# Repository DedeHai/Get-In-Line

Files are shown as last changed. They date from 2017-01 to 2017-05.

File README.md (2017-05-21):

# Get In Line - line-following robot
Simple line following robot using a single break-away PCB design. Using mostly 0805-components to make it easier to solder by hand. Four potentiometers at the bottom let you change the speed and regulator settings without re-programming the microcontroller. 
More information available at https://bashtelorofscience.wordpress.com/ 

License:
Software under MIT license
Hardware under Creative Commons 4.0 license: CC-BY-NC-SA

# Software
The PCB was designed in **eagle** version 7.5.0. The firmware project was created using **System Workbench for STM32** and **STM32CubeMX**.

# Fotos
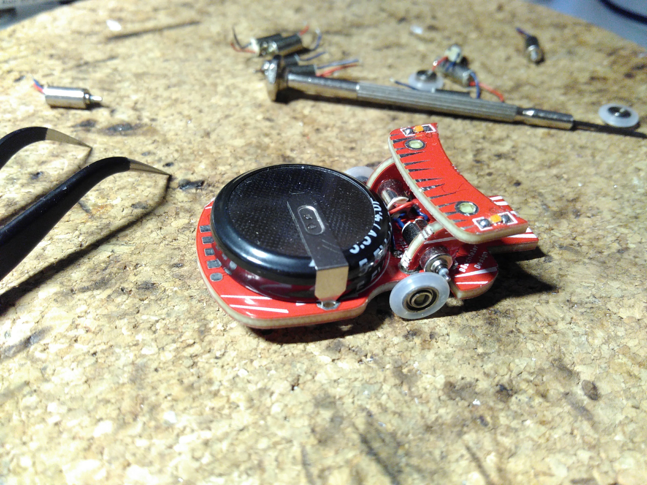
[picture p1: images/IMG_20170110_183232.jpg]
First Prototype Top
 
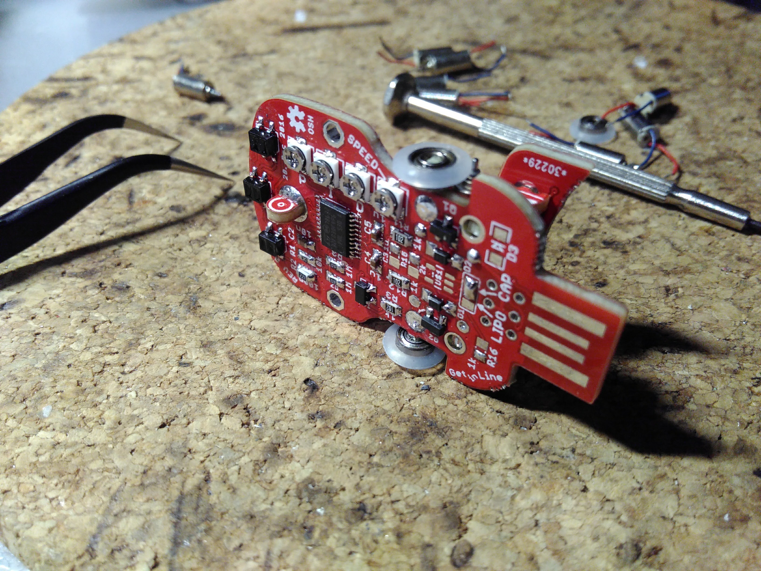
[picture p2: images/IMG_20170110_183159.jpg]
First Prototype Bottom
 
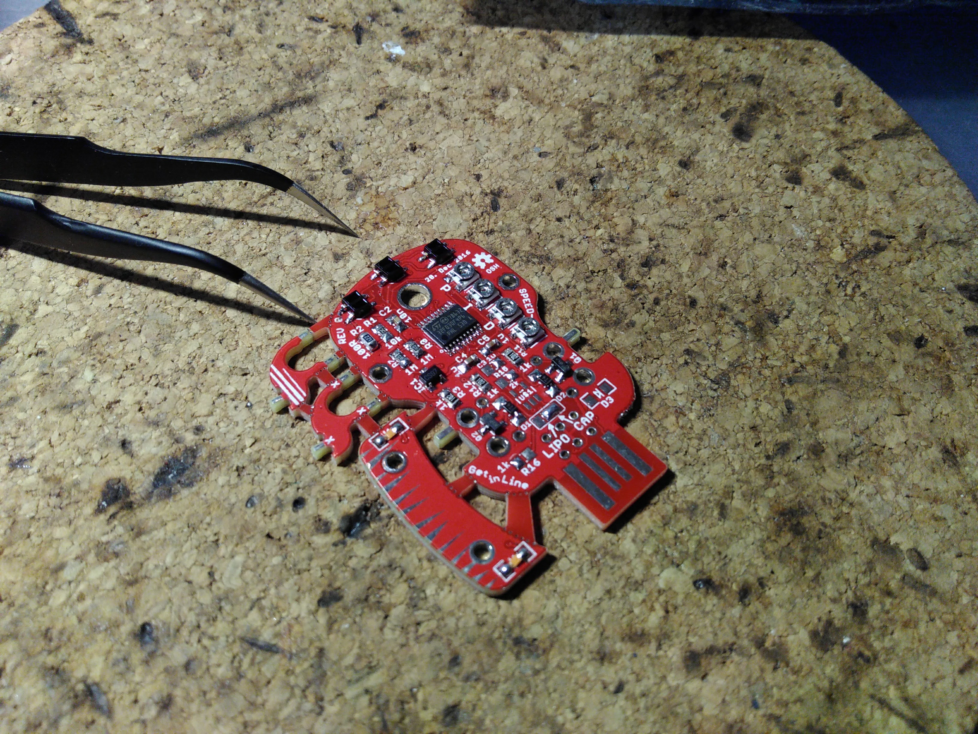
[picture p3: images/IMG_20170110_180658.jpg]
First Prototype Soldered


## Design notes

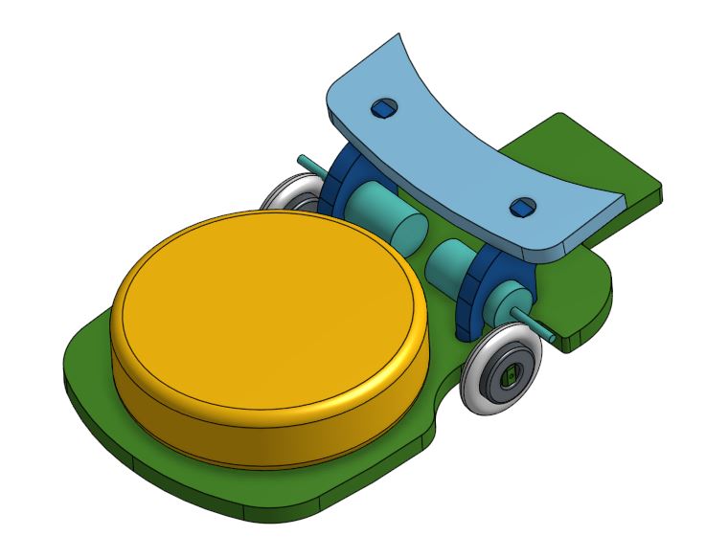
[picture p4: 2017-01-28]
Hardware/Get_In_Line_REV0_3D-view-mechanical.JPG

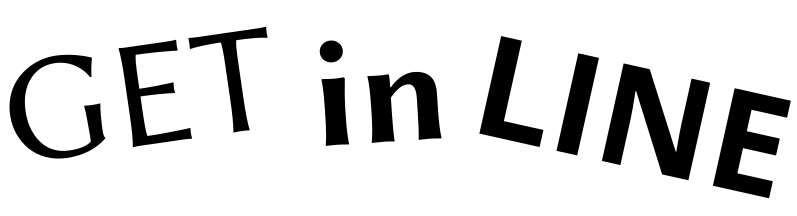
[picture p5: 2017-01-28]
Hardware/getinline.PNG

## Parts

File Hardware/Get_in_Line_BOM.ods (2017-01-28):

GET IN LINE – line follower robot Bill of Materials
Part | Order price | Pieces per order | Piecer per bot | Price per bot
PCB | 15 | 10 | 1 | 1.5 | http://dirtypcbs.com/store/pcbs
Bearings – MR52ZZ | 3.41 | 10 | 2 | 0.68 | http://www.banggood.com/10pcs-MR52ZZ-Double-Shielded-Deep-Groove-Ball-Miniature-Bearings-p-78792.html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
Rubber O ring | 2.38 | 150 | 2 | 0.03 | http://www.banggood.com/150pcs-White-O-Ring-Keycap-Rubber-For-Cherry-MX-Switch-Keyboard-p-937511.html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
Motor | 4.16 | 10 | 2 | 0.83 | http://www.banggood.com/10pcs-4x8mm-DC1_5-3V-Micro-Coreless-Motor-Vibration-Motor-p-999837.html?rmmds=myorder
Motor, better quality | 7 | 10 | 2 | 1.4 | https://www.aliexpress.com/item/good-quality-10pcs-408-dc-Coreless-Motor-for-helicopter-ailplanes-aircraf-high-speed-4x8mm/32261734792.html
Switch | 1.87 | 20 | 1 | 0.09 | https://www.aliexpress.com/item/WSFS-Wholesale-2-X-20-Pcs-On-Off-On-DPDT-2P2T-6-Pin-Vertical-DIP-Slide/32578250645.html
Trimmer Potentiometer | 4.7 | 50 | 4 | 0.38 | https://www.aliexpress.com/store/product/100PCS-3-3-3-3-3x3-5K-ohm-patch-adjustable-potentiometer/511081_32583469520.html
QRE1113 Reflective Sensor | 11 | 50 | 3 | 0.66 | https://www.aliexpress.com/item/Free-shipping-100pcs-lot-QRE1113GR-QRE1113-QRE1113G-SENSOR-OPTO-TRANS-REFL-SMD-PHOTO-Best-quality/32760197560.html
NPN transistor | 1.27 | 100 | 2 | 0.03 | https://www.aliexpress.com/item/Y111-MMBT2222A-100-PCS-SOT-23-MMBT2222-2N2222-SMD-General-Purpose-Transistors-NPN-40V-0-6A/32311239794.html
1N4148 Diode | 0.6 | 100 | 2 | 0.01 | https://www.aliexpress.com/item/Free-Shipping-100pcs-1N4148-LL4148-SMD-SMT-Diode-Switching-Signal/664923038.html
XC6206P332 3.3V Regulator | 1.4 | 50 | 1 | 0.03 | https://www.aliexpress.com/item/50pcs-free-shipping-XC6206P332MR-662K-XC6206-3-3V-0-5A-Positive-Fixed-LDO-Voltage-Regulator-SOT/32426685794.html
Resistor, 1k | 0.42 | 100 | 4 | 0.02 | https://www.aliexpress.com/store/product/100pcs-lot-SMD-Chip-Resistor-1-0805-1K-1K-1-8W-100-YAGEO-New-Original-Chip/1361740_32570151447.html
Resistor, 10k | 0.42 | 100 | 1 | 0 | https://www.aliexpress.com/store/product/100pcs-lot-SMD-Chip-Resistor-1-0805-10K-1-8W-100-YAGEO-New-Original-Chip-Fixed/1361740_32569368590.html
Resistor, 1M | 0.42 | 100 | 2 | 0.01 | https://www.aliexpress.com/store/product/100pcs-lot-SMD-Chip-Resistor-1-0805-1M-1-8W-100-YAGEO-New-Original-Chip-Fixed/1361740_32569356535.html
Resistor, 100R | 0.42 | 100 | 1 | 0 | https://www.aliexpress.com/store/product/100pcs-lot-SMD-Chip-Resistor-1-0805-100R-100-OHMS-1-8W-100-YAGEO-New-Original/1361740_32568098663.html
Resistor, 2k | 0.42 | 100 | 1 | 0 | https://www.aliexpress.com/store/product/100pcs-lot-SMD-Chip-Resistor-1-0805-2K-2K-1-8W-100-YAGEO-New-Original-Chip/1361740_32569396331.html
Capacitor, 100nF | 0.6 | 100 | 1 | 0.01 | https://www.aliexpress.com/store/product/Free-shipping-100pcs-lot-0805-100nF-104K-0-1uF-50V-X7R-10-2012-SMD-Multilayer-Ceramic/1361740_32677815090.html
Capacitor, 10uF, 10V | 1.82 | 100 | 3 | 0.05 | https://www.aliexpress.com/store/product/Free-shipping-100pcs-lot-0805-10uF-106K-25V-X7R-10-2012-SMD-Multilayer-Ceramic-Chip-Capacitor/1361740_32677028139.html
LED 1206 (any color) | 1.43 | 100 | 3 | 0.04 | https://www.aliexpress.com/item/100pcs-lot-1206-SMD-LED-light-Package-LED-Package-Red-White-Green-Blue-Yellow-1206-led/32668226209.html
STM32F03F4P6 Microcontroller | 4.3 | 10 | 1 | 0.43 | https://www.aliexpress.com/item/Free-shipping-10pcs-Lot-STM32F030F4P6-STM32F030F/1899750362.html
TP4054 LiPo Charger | 3.6 | 20 | 1 | 0.18 | https://www.aliexpress.com/item/TP4054-new-original-printing-54b-lithium-rechargeable-IC-package-SOT23-5-SZHQDZ/32712500075.html
LiPo Battery (20x30mm max size) | 14 | 10 | 1 | 1.4 | https://www.aliexpress.com/item/3-7V-150mAh-Syma-S107-S107G-1S-3-7V-150mAh-Li-Po-Battery-3-7V-Helicopter/32752994770.html
 | 80.64 |  |  | 7.79
Optional
Programmer
ST-Link clone (Programmer) | 2.2 | 1 |  |  | https://www.aliexpress.com/item/Hot-Sale-1PCS-ST-LINK-Stlink-ST-Link-V2-Mini-STM8-STM32-Simulator-Download-Programmer-Programming/32343514985.html
SuperCap (very short working time!) | 2.76 | 2 | 1 | 1.38 | https://www.aliexpress.com/item/2Pcs-ultra-capacitor-5-5v4f-super-capacitor-H-style-For-promotion-Now-Lowest-Price/32571210201.html
Resistors, various (kit) | 2.2 | 50 | 15 | 0.66 | https://www.aliexpress.com/item/Free-shipping-0805-5-SMD-Resistor-Kit-0R-10M-36valuesX20pcs-720pcs-Chip-Resistor-sample-kit/32695511447.html
Capacitor, various (kit) | 2.7 | 10 | 2 | 0.54 | https://www.aliexpress.com/item/Free-shipping-0805-SMD-Capacitor-29valuesX10pcs-290pcs-Chip-Capacitor-Electronic-Components-Package-Samples-kit/773778463.html

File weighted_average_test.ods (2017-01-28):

Position | Value | Weighted value
7500 | 200 | 1500000
15000 | 400 | 6000000
22500 | 135 | 3037500
 |  |  | Line center position:
sum: | 735 | 10537500 | 14336.7346938776
Center aligned:
-7500
0
7500 |  |  | -663.2653061224

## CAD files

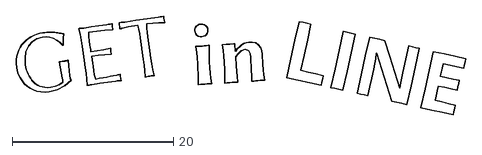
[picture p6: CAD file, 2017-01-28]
Hardware/getinline_writing.dxf
55.8 x 12.3

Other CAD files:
Hardware/getinline.dxf

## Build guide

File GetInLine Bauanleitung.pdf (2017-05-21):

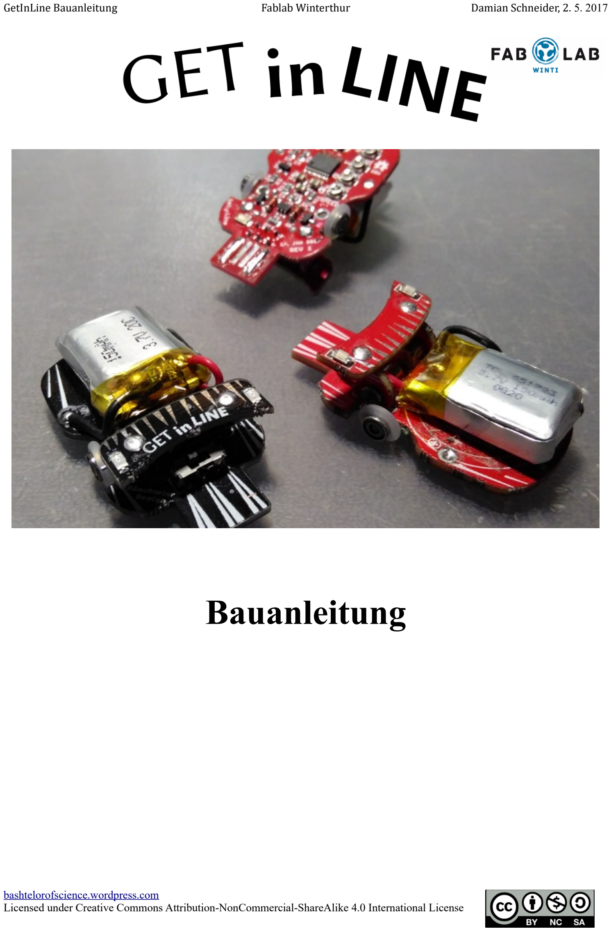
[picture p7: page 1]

GetInLine Bauanleitung | Fablab Winterthur | Damian Schneider, 2. 5. 2017

# Bauanleitung

bashtelorofscience.wordpress.com
Licensed under Creative Commons Attribution-NonCommercial-ShareAlike 4.0 International License

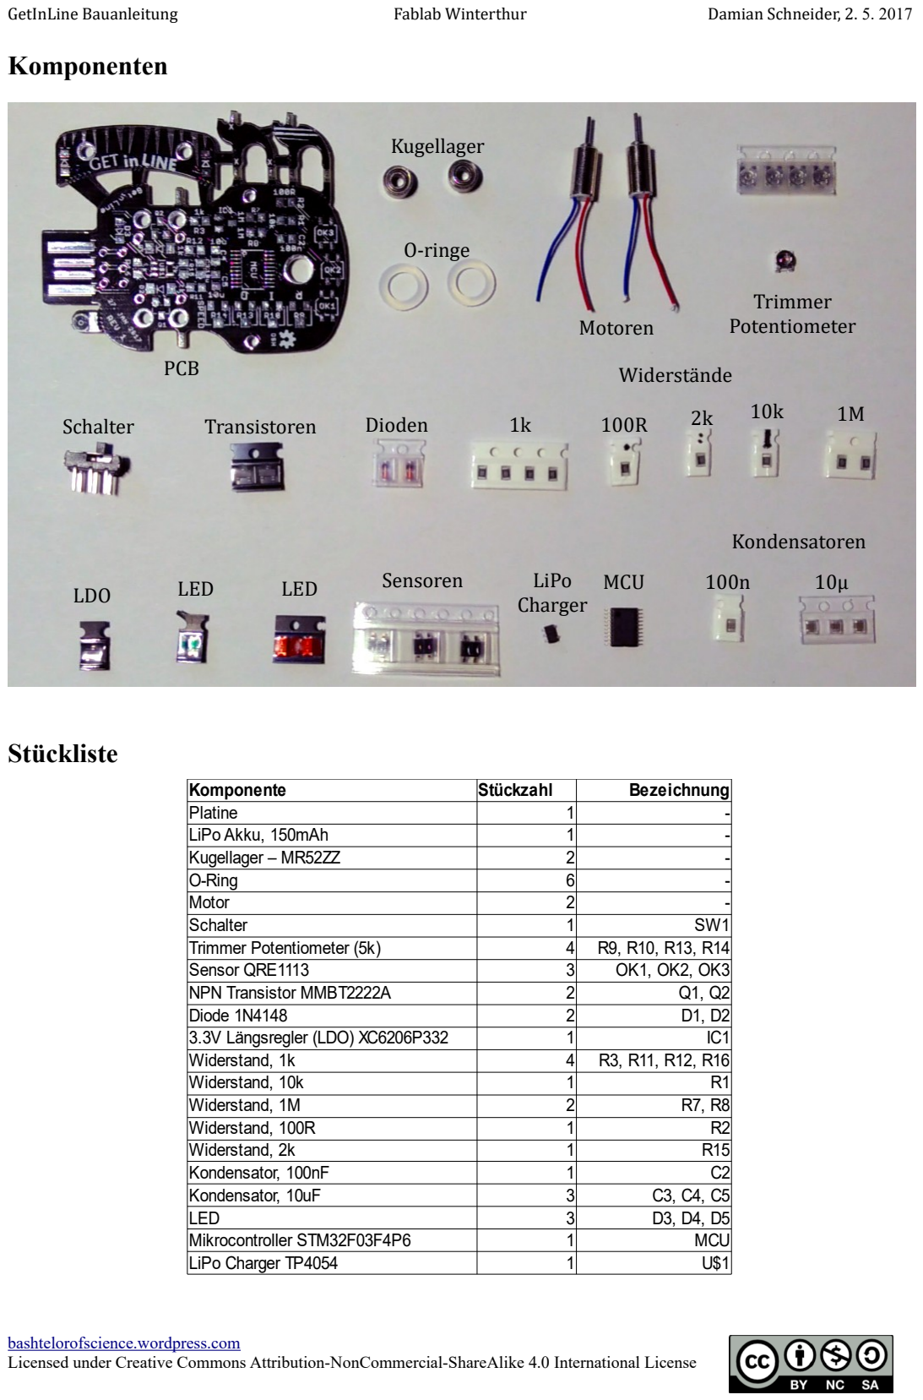
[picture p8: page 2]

Komponenten

Stückliste

bashtelorofscience.wordpress.com

Komponente | Stückzahl | Bezeichnung
Platine | 1 | -
LiPo Akku, 150mAh | 1 | -
Kugellager – MR52ZZ | 2 | -
O-Ring | 6 | -
Motor | 2 | -
Schalter | 1 | SW1
Trimmer Potentiometer (5k) | 4 | R9, R10, R13, R14
Sensor QRE1113 | 3 | OK1, OK2, OK3
NPN Transistor MMBT2222A | 2 | Q1, Q2
Diode 1N4148 | 2 | D1, D2
3.3V Längsregler (LDO) XC6206P332 | 1 | IC1
Widerstand, 1k | 4 | R3, R11, R12, R16
Widerstand, 10k | 1 | R1
Widerstand, 1M | 2 | R7, R8
Widerstand, 100R | 1 | R2
Widerstand, 2k | 1 | R15
Kondensator, 100nF | 1 | C2
Kondensator, 10uF | 3 | C3, C4, C5
LED | 3 | D3, D4, D5
Mikrocontroller STM32F03F4P6 | 1 | MCU
LiPo Charger TP4054 | 1 | U$1

Kugellager

O-ringe

PCB

Motoren

Trimmer
Potentiometer
Schalter | Transistoren | Dioden

Widerstaände
1k | 100R | 2k | 10k | 1M

Kondensatoren
LiPo | MCU | 100n | 10µ
Charger

Sensoren
LDO | LED | LED

Bestückungsplan

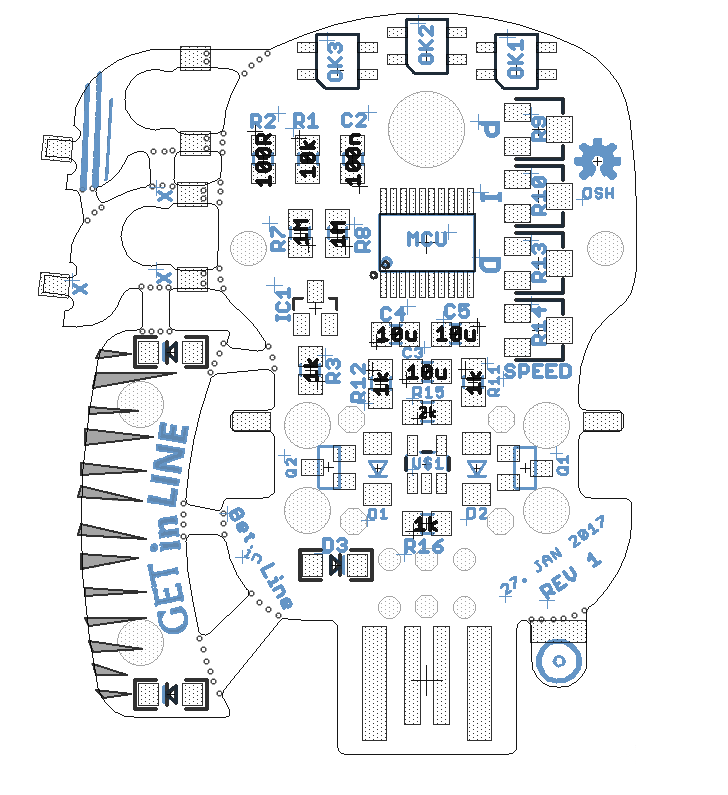
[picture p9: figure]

bashtelorofscience.wordpress.com

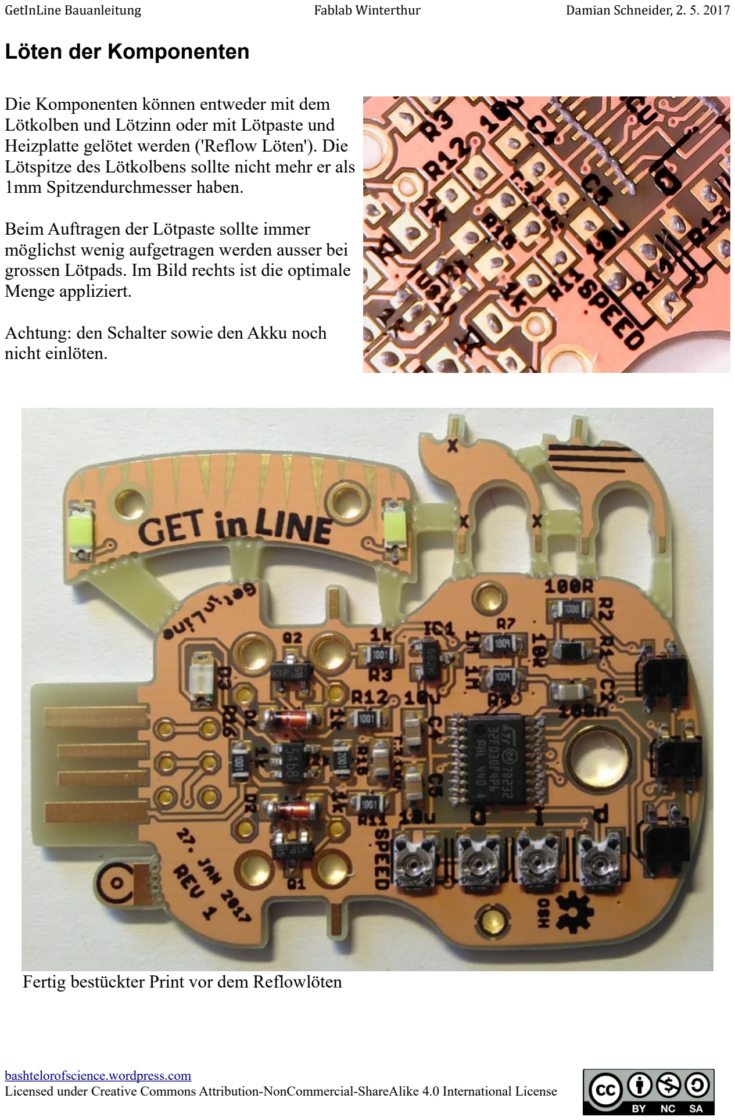
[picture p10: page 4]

Löten der Komponenten

Die Komponenten können entweder mit dem Lötkolben und Lötzinn oder mit Lötpaste und Heizplatte gelötet werden ('Reflow Löten'). Die Lötspitze des Lötkolbens sollte nicht mehr er als 1mm Spitzendurchmesser haben.

Beim Auftragen der Lötpaste sollte immer möglichst wenig aufgetragen werden ausser bei grossen Lötpads. Im Bild rechts ist die optimale Menge appliziert.

Achtung: den Schalter sowie den Akku noch nicht einlöten.

Fertig bestückter Print vor dem Reflowlöten

bashtelorofscience.wordpress.com

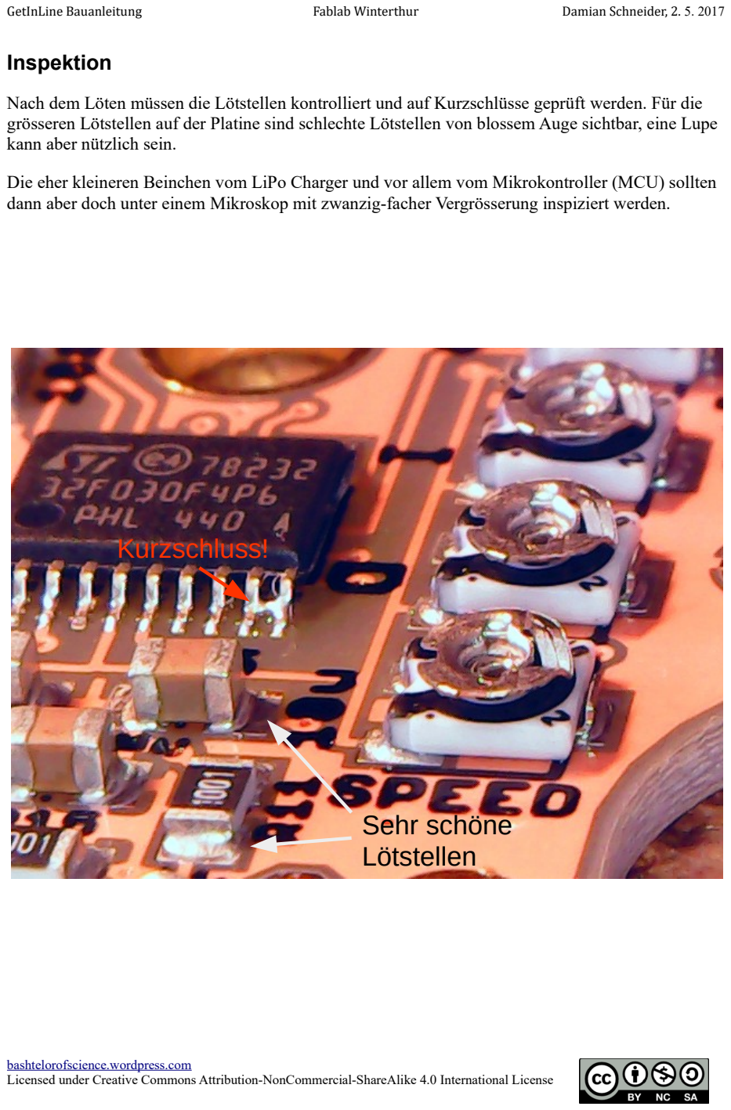
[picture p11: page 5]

Inspektion

Nach dem Löten müssen die Lötstellen kontrolliert und auf Kurzschlüsse geprüft werden. Für die grösseren Lötstellen auf der Platine sind schlechte Lötstellen von blossem Auge sichtbar, eine Lupe kann aber nützlich sein.

Die eher kleineren Beinchen vom LiPo Charger und vor allem vom Mikrokontroller (MCU) sollten dann aber doch unter einem Mikroskop mit zwanzig-facher Vergrösserung inspiziert werden.

bashtelorofscience.wordpress.com

## Kurzschluss!

## Sehr schöne Lötstellen

Roboter Montage
Bitte jeden Abschnitt zuerst komplett durchlesen und erst dann ausführen um mühsames Entlöten oder gar Zerstörung des Prints zu vermeiden.
Als erstes müssen die einzelnen Teile der Platine vorsichtig auseinander gebrochen werden. Die feineren Stege knippst man am einfachsten mit einem feinen Seitenschneider möglichst nahe an der Hauptplatine durch. Die perforierten stellen können auch gebrochen werden, dazu sollte man immer zwei Zangen verwenden um die dünnen Teile nicht zu verbiegen oder gar zu brechen. Die etwas unschönen Bruchstellen können gut mit einer Schlüsselfeile oder mit einem Messer nachbearbeitet werden.

Vorderrad einlöten: mit dem Print auf der Lötunterlage das Rad wie in den Bildern gezeigt ausrichten und mit viel Lötzinn einlöten. Dabei ist darauf zu achten, dass das Lötzinn sowohl das Loch wie auch das 'Rad' gut benetzt.

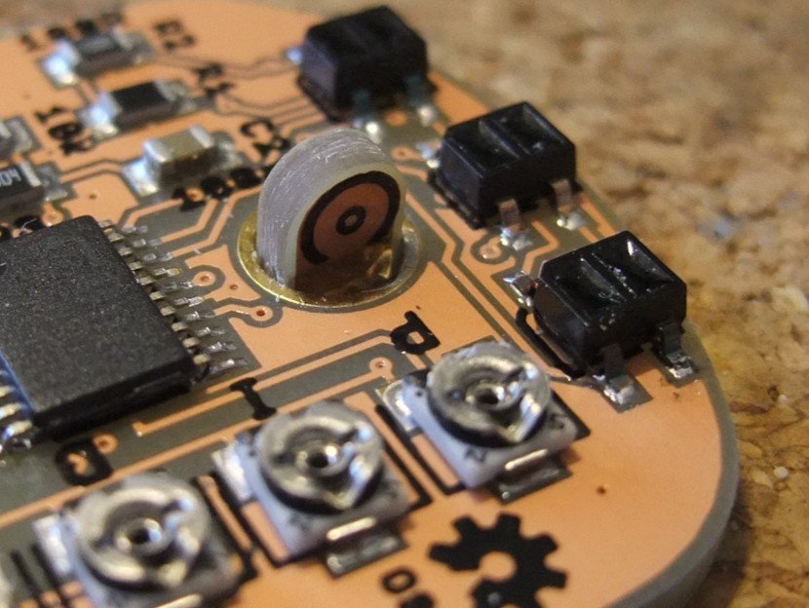
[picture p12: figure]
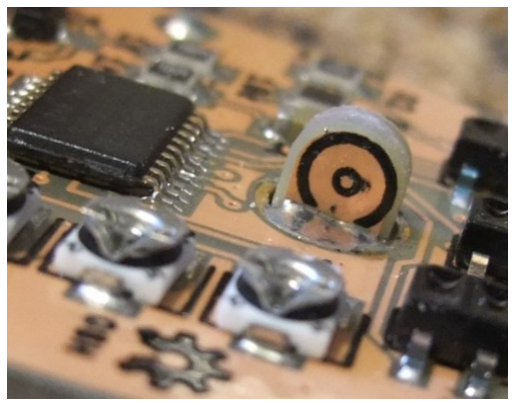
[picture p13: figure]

Vorderrad ausgerichtet… | …und gelötet

Spoiler Ausrichten: die beiden Seitenwände entsprechend den Markierungen X und Y einstecken und den Spoiler oben drauf montieren. Sobald alles schön passt kann der Spoiler von oben an die Seitenwände angelötet werden. Dabei ist es wichtig genügen lange mit dem Lötkolben zu heizen. Die Seitenwände nicht mit der Hauptplatine verlöten! Jetzt wird der Spoiler zusammen mit den Seitenwänden wieder entfernt um die Motoren einzusetzen.

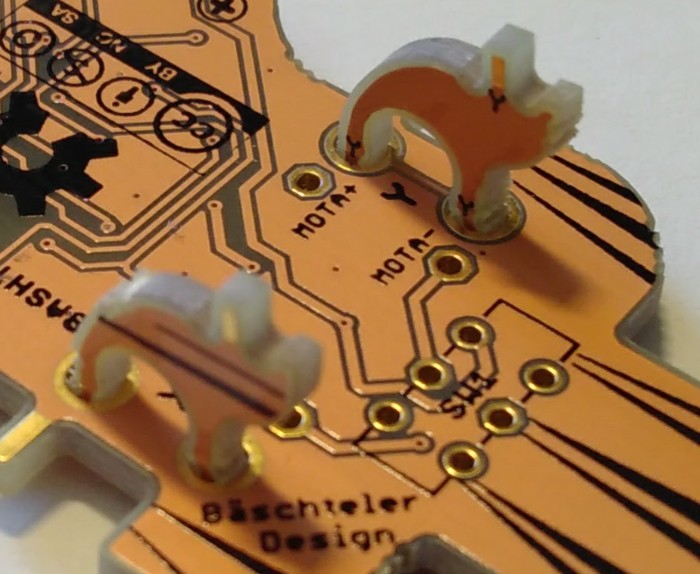
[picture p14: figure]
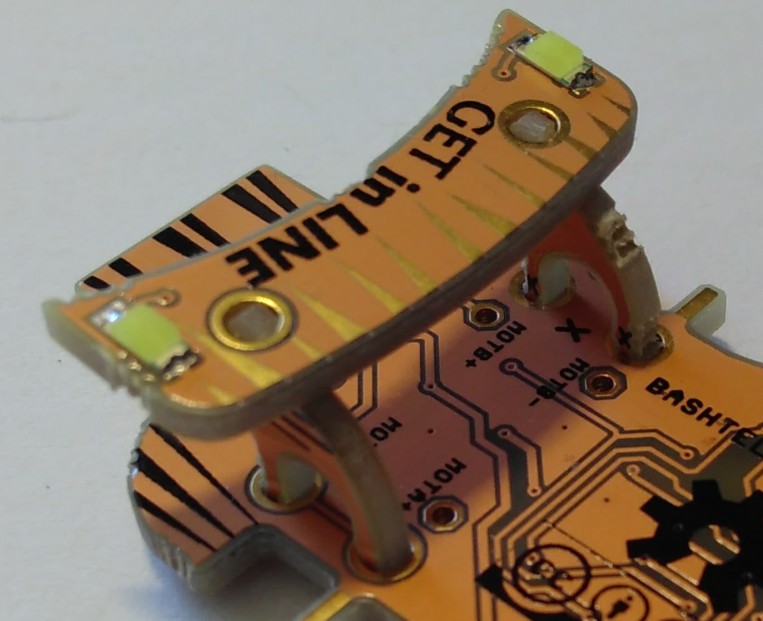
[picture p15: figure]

Positionieren der Seitenwände und des Spoilers

Schalter löten: der Schalter kommt auf die Oberseite, da wo der Print mit ‚SW1‘ markiert ist.

bashtelorofscience.wordpress.com

Motoren einsetzen: die Kabel der Motoren auf eine Länge von ca. 2cm kürzen, abisolieren und verzinnen. Danach beide Motoren von aussen her in die Öffnungen der Seitenwände einschieben. Das benötigt etwas kraft. Vorsicht: die dünnen Beine der Seitenwände brechen leicht ab. Die Motoren vorerst etwa mittig platzieren und so drehen, dass die Kabel wie auf dem Bild gezeigt ausgerichtet sind (nicht an den kabeln ziehen!). Jetzt können die Kabel eingelötet werden. Dabei die Polarität beachten: blau auf minus, rot auf plus, wie im rechten Foto.

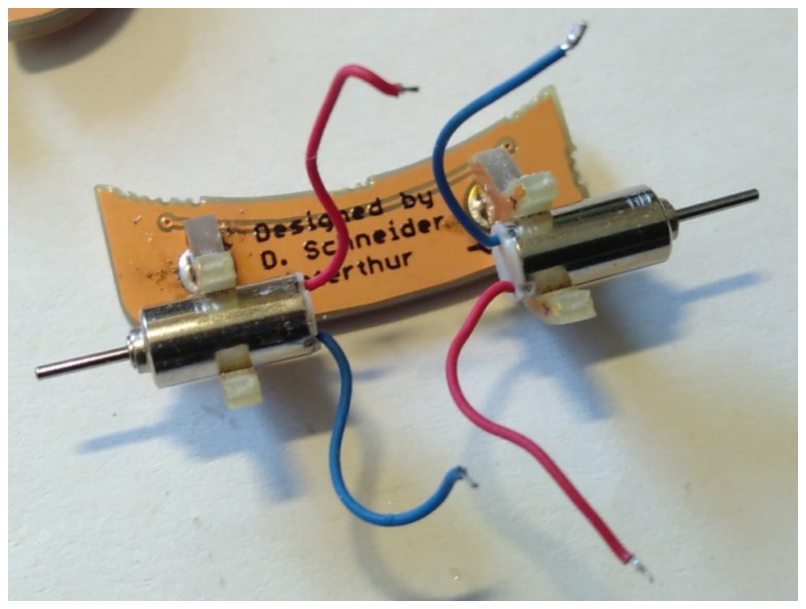
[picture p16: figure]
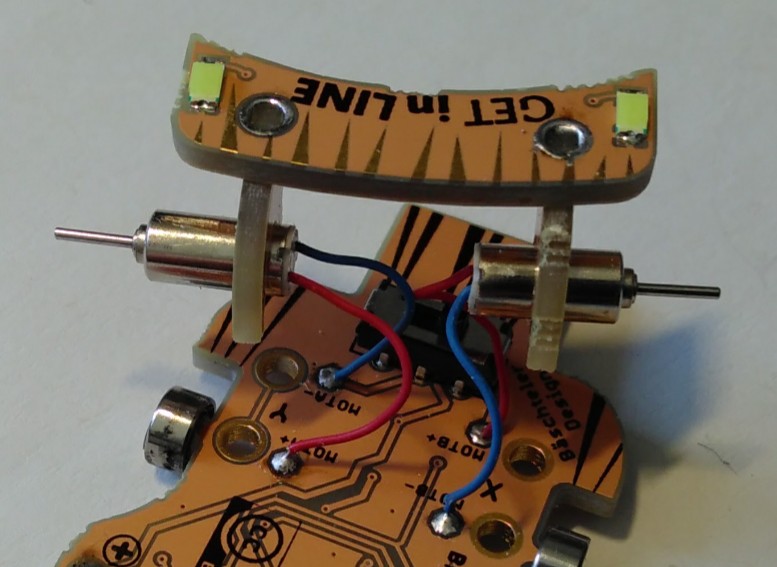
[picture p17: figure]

Motoren eingesetzt, Kabel ausgerichtet | und eingelötet

Akku löten: Den Schalter auf Position ‚Aus‘ stellen (wie im Foto unten). Den Akku mit der richtigen Polarität einlöten. Die Isolation am positiven Kabel erst kurz vor dem Löten des Kabels entfernen, der Akku hat viel Leistung und kann bei Kurzschlüssen über die Platine auch Leiterbahnen schmelzen!
Kugellager einpressen: die beiden Kugellager können einfach mit etwas Kraftaufwand aufgesteckt werden und sollten dann gut halten. Allenfalls mit einem Zahnstocher ganz wenig Sekundenkleber auftragen.

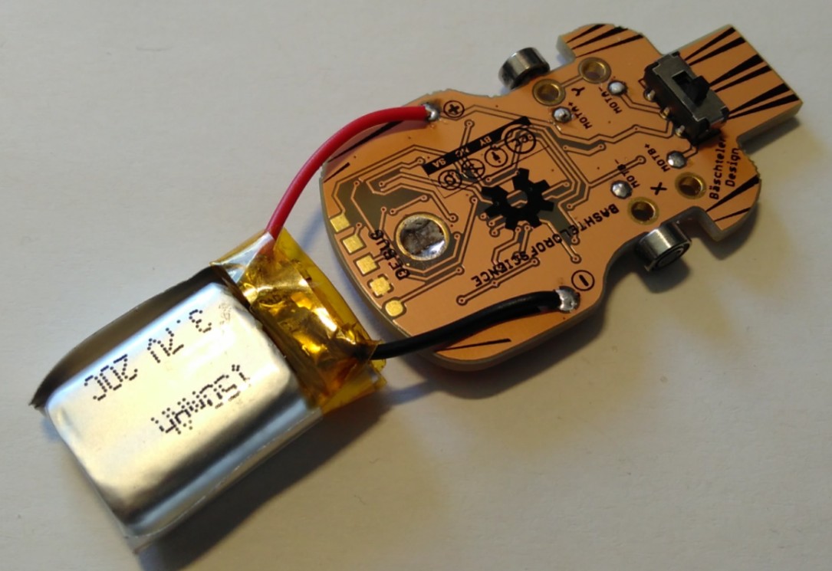
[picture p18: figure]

Schalter und Akku angelötet, Kugellager aufgesetzt (Motoren fehlen auf dem Bild)

bashtelorofscience.wordpress.com

O-Ringe aufsetzen: aus den O-ringen zwei auswählen die möglichst keine Brauen auf der Lauffläche haben und auf die Kugellager aufsetzen. Brauen allenfalls mit einer Pinzette entfernen.

Drehrichtung prüfen: den Roboter einschalten und die Motoren von Hand leicht auf die O-ringe drücken. Die Drehrichtung der Räder muss so sein, wie es in den Abbildungen mit Pfeilen angedeutet ist. Der Roboter soll sich ja später vorwärts bewegen. Stimmt die Drehrichtung nicht müssen die Motoranschlüsse andersrum gelötet werden.

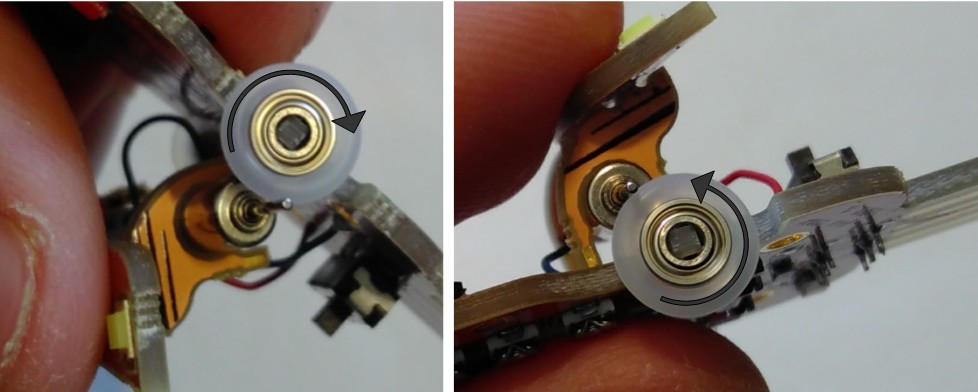
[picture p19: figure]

Motortest: Drehrichtungen

Motren ausrichten: Die Motoren werden in den Seitenwänden so ausgerichtet, dass sie aussen bündig sowie gerade und auf einer Linie sind (siehe Foto). Die Motorkabel alle nach aussen biegen, damit sie beim Einsetzen nicht unter die Motoren zu liegen kommen. Jetzt kann die Motoreinheit eingesetzt werden. An dieser Stelle ist es wichtig, die Anpresskraft der Motoren auf die O-Ringe möglichst gut einzustellen. Kleine Korrekturen sind zwar später noch möglich aber je besser die Motoreinheit vor dem Verlöten ausgerichtet ist, desto besser funktioniert am Ende der Roboter.
Die Motoren müssen auf der Platine aufliegen.

Einstellen der Anpresskraft: dieser Schritt ist entscheidend damit der Roboter gut funktioniert. Wenn die Motoreinheit richtig sitzt kann die Anpresskraft durch kippen eingestellt werden. Die Kraft sollte so gering wie möglich sein aber nicht so, dass beim Stoppen des Rads von Hand der Motor durchdreht und nicht so stark, dass der Motor nach dem Stoppen nicht selbständig wieder anläuft. Wenn die Motoren auf einer Linie ausgerichtet wurden sollte es möglich sein, beide Seiten gleichzeitig auszurichten.

bashtelorofscience.wordpress.com

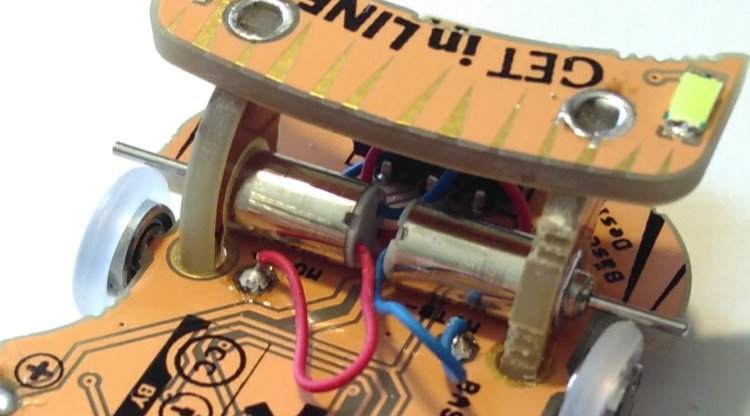
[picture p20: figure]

Anpressdruck gut eingestellt

Seitenwände Löten: mit laufenden Motoren den Roboter vorsichtig mit dem Spoiler nach unten auf die Lötunterlage legen. Die Anpresskraft noch einmal überprüfen (Räder stoppen). Die beiden Lötstellen die mit grünen Pfeilen Markiert sind löten (eventuell grössere Lötspitze benutzen) und dabei möglichst keine Kraft aufwenden, ansonsten wird die Motoreinheit verschoben und muss wieder ausgerichtet werden. Achtung: werden auch die Lötstellen mit den roten Kreuzen gelötet, ist ein erneutes ausrichten der Motoren schwierig. Beim Löten genügend Lötzinn verwenden und mindestens 5 Sekunden aufheizen. Beim löten der zweiten Seitenwand sollten die beiden LEDs auf dem Spoiler anfangen zu leuchten.

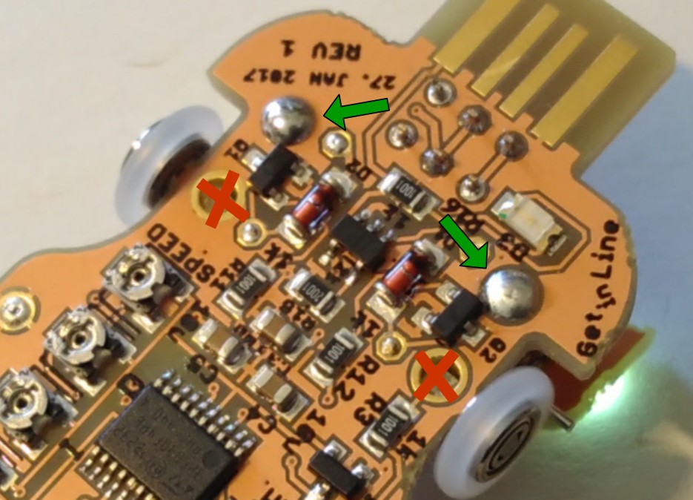
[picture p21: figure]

Seitenwände gelötet und die LEDs leuchten bereits

Erste Testfahrt: Jetzt kannst du den Akku richtig platzieren und schon kanns los gehen mit der ersten Testfahrt. Schalte den Roboter aus und setzte ihn auf eine Teststrecke. Bei jedem Einschalten

bashtelorofscience.wordpress.com werden die Sensoren automatisch kalibriert. Wenn alles gut funktioniert und kein weiteres Ausrichten der Motoren nötig ist können nun auch noch die anderen beiden Lötstellen der Seitenwände gelötet werden.

Letze Anpassungen: wenn alles ok ist, kannst du jetzt die zweite Lötstelle der Seitenwände verlöten. Auch hier wieder genügend Zinn verwenden und mindestens 5 Sekunden heizen. Die Anpresskraft kann nun noch folgendermassen Feinjustiert werden: mit einem kleinen Schraubenzieher (nicht mit der Pinzette!) auf den Motor drücken, bis die Anpresskraft stimmt. Achtung: nicht auf die Kabel drücken, diese können schnell reissen.
Den Akku klebt man am besten mit doppelseitigem Klebeband fest oder mit etwas Heissleim. Damit das Aufladen am USB-Port gut funktioniert müssen noch die beiden äusseren Pads vom USB-Stecker dick verzinnt werden.

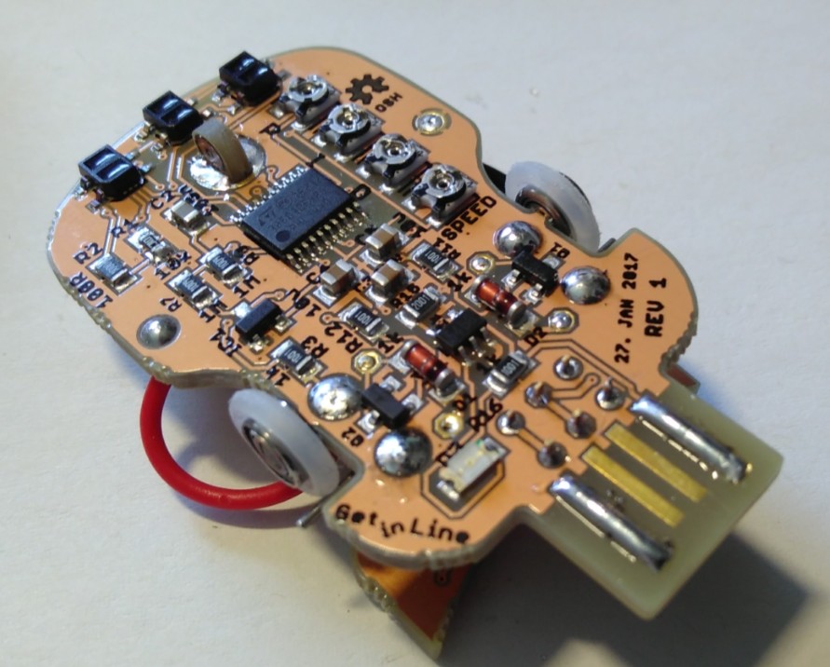
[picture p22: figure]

Fertig zusammengebauter Roboter

Einstellen der Regelung
Mit allen Potentiometer auf Mittelstellung fährt der Roboter eigentlich schon ganz gut. Man kann die Regelung aber auch noch optimieren damit der Roboter möglichst schnell oder möglichst ruhig fährt.

bashtelorofscience.wordpress.com

Die Potentiometer sind mit P, I, D und SPEED angeschrieben.

P: Proportional Anteil des Reglers - Gegensteuer bei Abweichung vom Sollsignal. Zu hoch und der Roboter oszilliert mit schnellen Schwenkern. Wenn der Wert zu tief ist übernimmt der Integral Anteil die Regelung und der Roboter 'schlängelt' über den Pfad.

I: Integralanteil des Reglers - die Regelabweichung wird aufsummiert um kleine Fehler zu korrigieren, auf die der proportionale Anteil zu wenig reagiert.

D: Differentialanteil des Reglers - dieser beugt Übersteuerungen vor und dämpft Oszillationen etwas indem er kurzfristig dem Integralanteil entgegenwirkt.

SPEED: das "Gaspedal". Ist die Geschwindigkeit zu tief eingestellt, fährt der Roboter gar nicht oder bleibt dauernd stehen. Zu hohe Geschwindigkeiten bereiten dem Regler mühe und in den Kurven schiesst er aus der Bahn - der Roboter hat keine Bremse! Für eine ruhige Fahrt sollte die Geschwindigkeit so tief wie möglich eingestellt sein.

bashtelorofscience.wordpress.com

## Appendix: SMD Bauteilgehäuse

SMD Komponenten kommen in hunderten von verschiedenen Gehäusen. Viele davon sind Genormt aber diverse Hersteller haben auch noch ihre eigenen Varianten davon, als Beispiel sei hier der Sensor QRE1113 von ON-Semiconductor (früher Fairchild) angeführt, der ein Spezialgehäuse gepackt ist.
Gehäuse von Widerständen, Kondensatoren und LEDs sowie weitere zweipolige Komponenten werden mit der Grössenangabe in hundertstel Zoll angegeben. Gängige Bauteilgrössen in Absteigender Reihenfolge sind 1210, 1206, 0805, 0603, 0402 und 0201. Bis zur Grösse von 0603 kann gut von Hand gelötet werden, 0402 geht gerade noch unter dem Mikroskop und bei 0201 wird’s eher knifflig, ist aber nicht unmöglich. Die hier verwendeten Widerstände und Kondensatoren sind in der Grösse 0805 (0.08x0.05 Zoll oder 2x1.27mm) und die LEDs sind in 1206 Gehäusen untergebracht.
Symmetrische Bauteile die eine Ausrichtung benötigen haben immer eine Kennzeichnung an einem der Anschlüsse. Fast ausnahmslos ist Pin eins mit einem Punkt oder einer angeschrägten Ecke oder Kante markiert. Bei LEDs ist häufig die Kathode mit einem grünen Punkt markiert oder man findet ein Symbol auf der Unterseite (oder beides). Bei asymmetrischen Bauteilen ist die Ausrichtung ohnehin klar und eine Markierung ist optional.

Widerstände
Bei Widerständen gibt es bei SMD Bauteilen im Gegensatz zur bedrahteten Version keine Farbcodes mehr. Stattdessen ist der Widerstandswert in Zahlen aufgedruckt. Dabei bezeichnen die ersten Ziffern den Widerstandswert und die letzte Ziffer die Zehnerpotenz. Für die hier abgebildeten Widerstände bedeutet dies:
1000 → 100*10⁰
= 100Ω
2001 → 200*10¹
= 2000Ω = 2kΩ
1004 → 100*10⁴
= 1000000Ω = 1MΩ

LED/Dioden

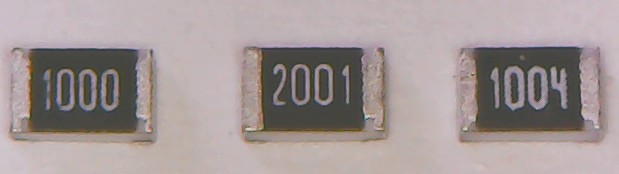
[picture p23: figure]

Dioden haben wie immer eine Markierung auf der Kathodenseite. Im allgemeinen ist dies eine Linie, kann aber auch ein Punkt sein. Bei LEDs gibt es oft (zusätzlich) ein 'Dreieck' Symbol auf der Unterseite, welches das Dreieck im Diodensymbol repräsentiert. Im nachfolgenden Bild ist die Kathode jeweils oben.

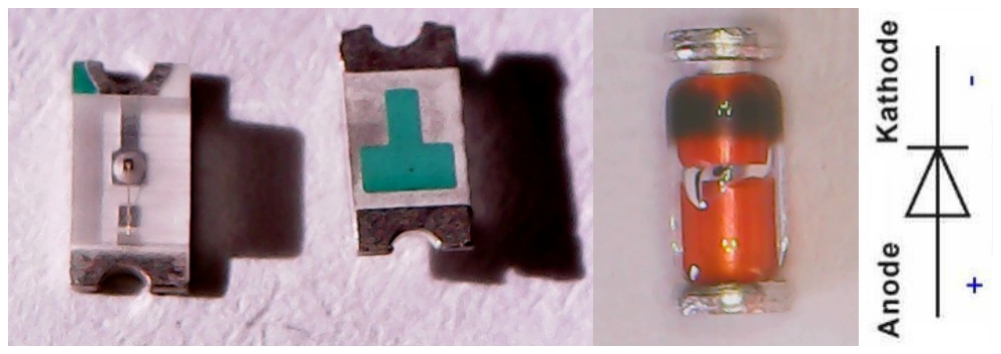
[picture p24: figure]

LED im 1206 und Diode im SOD80 Gehäuse

bashtelorofscience.wordpress.com

Mikrokontroller (MCU)
Als Beispiel für ein symmetrisches Gehäuse sei hier der verwendete Mikrokontroller STM32F03F4P4 angeführt. Die Gehäusebezeichnung ist TSSOP20.

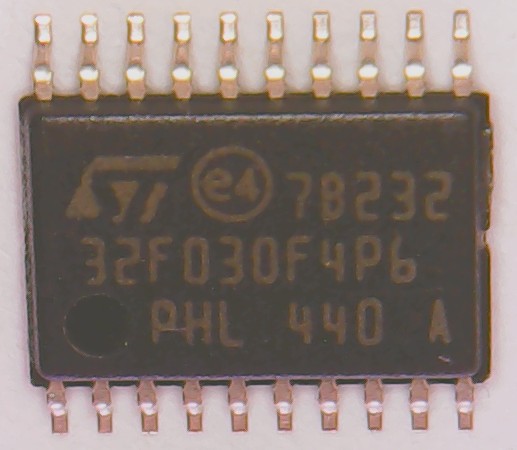
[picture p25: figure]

Pin 1 ist mit einem Punkt markiert

Weitere Typische Gehäuseformen
Es gibt wie bereits erwähnt eine Vielzahl von Gehäusetypen. Sehr einfach zu löten und hauptsächlich für Transistoren, Diodenarrays und LDOs verwendet ist die Bauform SOT23. Dieses gibt’s auch mit fünf Beinchen, das nennt sich dann SOT23-5.
Von den Arduino's kennt man das sehr weit verbreitete TQFP

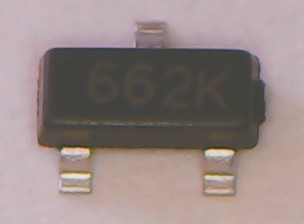
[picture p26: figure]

Package, das dem TSSOP gehäuse ähnlich ist, jedoch einen grösseren
Pinabstand (=pitch) hat (0.5mm vs. 0.4mm). Eher schwieriger zu
löten sind dann die moderneren Gehäuse ohne Beinchen: QFN oder noch kleiner: BGA. Diese können mit einem Lötkolben kaum oder gar nicht gelötet werden, mit Lötpaste und reflow-löten sind diese aber auch von Hand zu schaffen wenn man eine Lötpastenschablone benutzt.

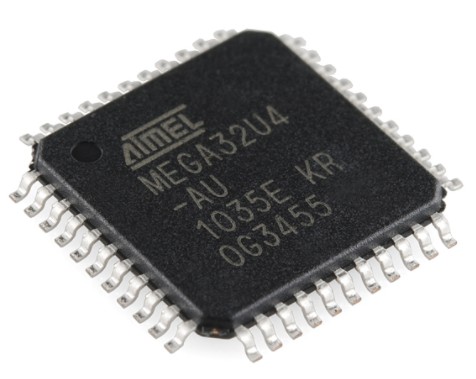
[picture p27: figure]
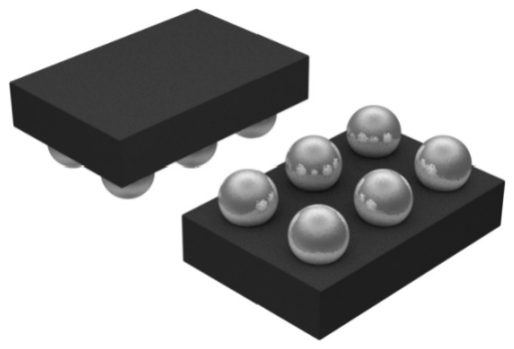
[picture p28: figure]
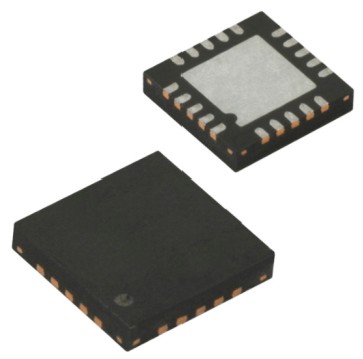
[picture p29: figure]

TQFP | QFN | BGA

bashtelorofscience.wordpress.com

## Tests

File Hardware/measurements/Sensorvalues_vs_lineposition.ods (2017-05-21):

sensorValues[0] | volatile uint16_t | 1872
sensorValues[1] | volatile uint16_t | 2237
sensorValues[2] | volatile uint16_t | 1751
sensorValues[0] | volatile uint16_t | 1484
sensorValues[1] | volatile uint16_t | 2126
sensorValues[2] | volatile uint16_t | 1876
sensorValues[0] | volatile uint16_t | 3131
sensorValues[1] | volatile uint16_t | 2247
sensorValues[2] | volatile uint16_t | 1851
sensorValues[0] | volatile uint16_t | 3374
sensorValues[1] | volatile uint16_t | 2234
sensorValues[2] | volatile uint16_t | 1838
Sensor Value outputs vs. Position on a 12mm wide line on white paper
sensorValues[0] | sensorValues[1] | sensorValues[2]
3430 | 2429 | 1972
3413 | 3693 | 1999
2543 | 3569 | 1912
1921 | 3527 | 3638
1967 | 3527 | 3687
1860 | 2967 | 3556
1890 | 2096 | 3116
1668 | 1996 | 1716
Position output vs Position on a 8mm line
lineposition
-100
-497
-1781
-1955
-1958
-768
107
29
358
1226
1732
1574
1624
493
-373

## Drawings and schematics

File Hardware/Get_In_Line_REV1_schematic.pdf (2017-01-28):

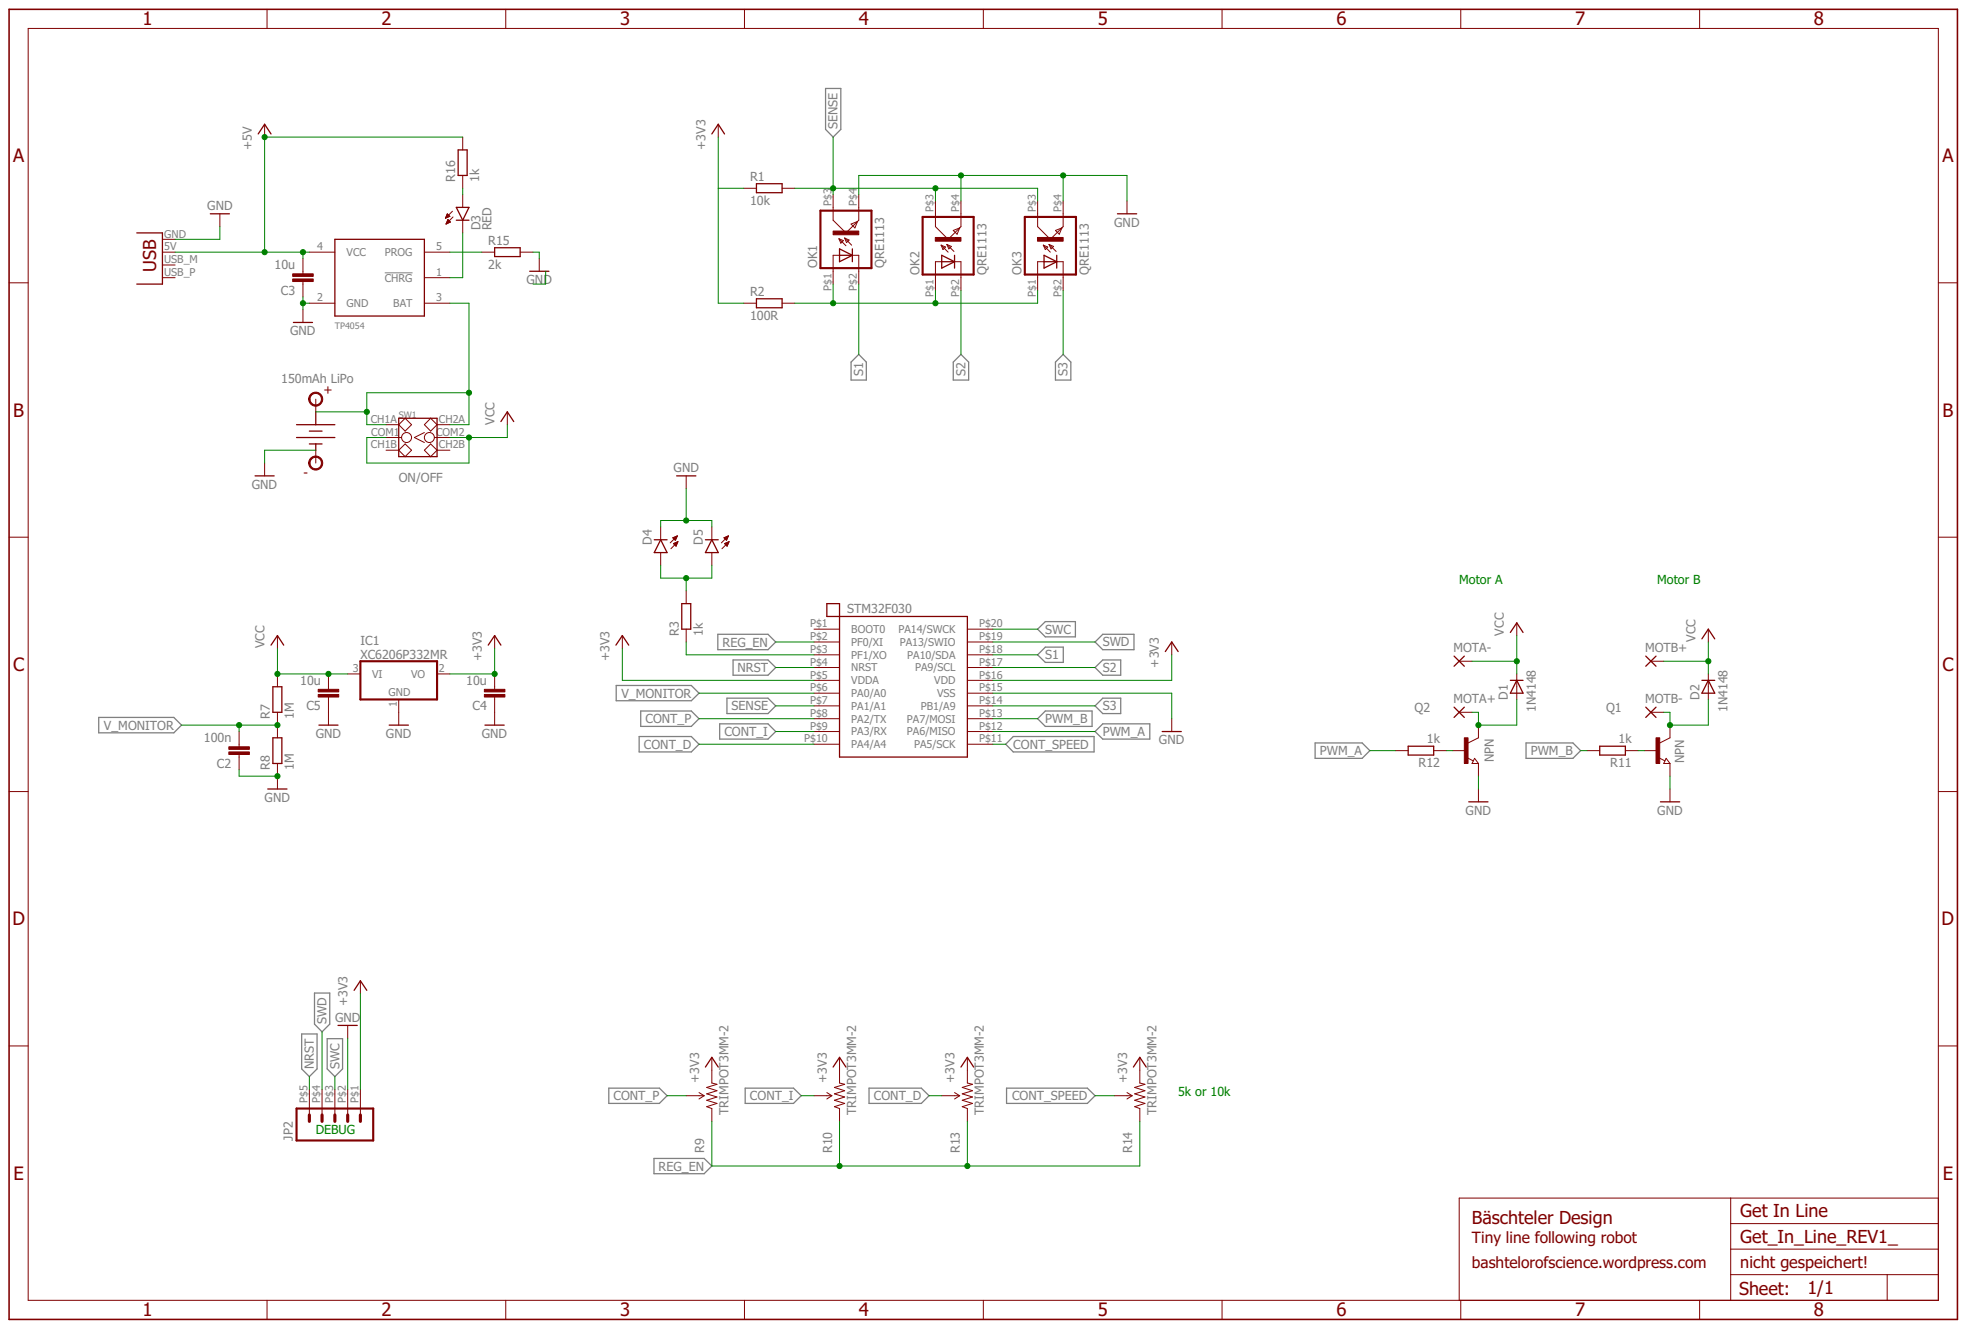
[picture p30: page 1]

V_MONITOR | P$15 VDD

P$12 PA7/MOSI P$13 PB1/A9 P$14 VSS

Tiny line following robot bashtelorofscience.wordpress.com | Get In Line Bäschteler Design

Sheet: 1/1

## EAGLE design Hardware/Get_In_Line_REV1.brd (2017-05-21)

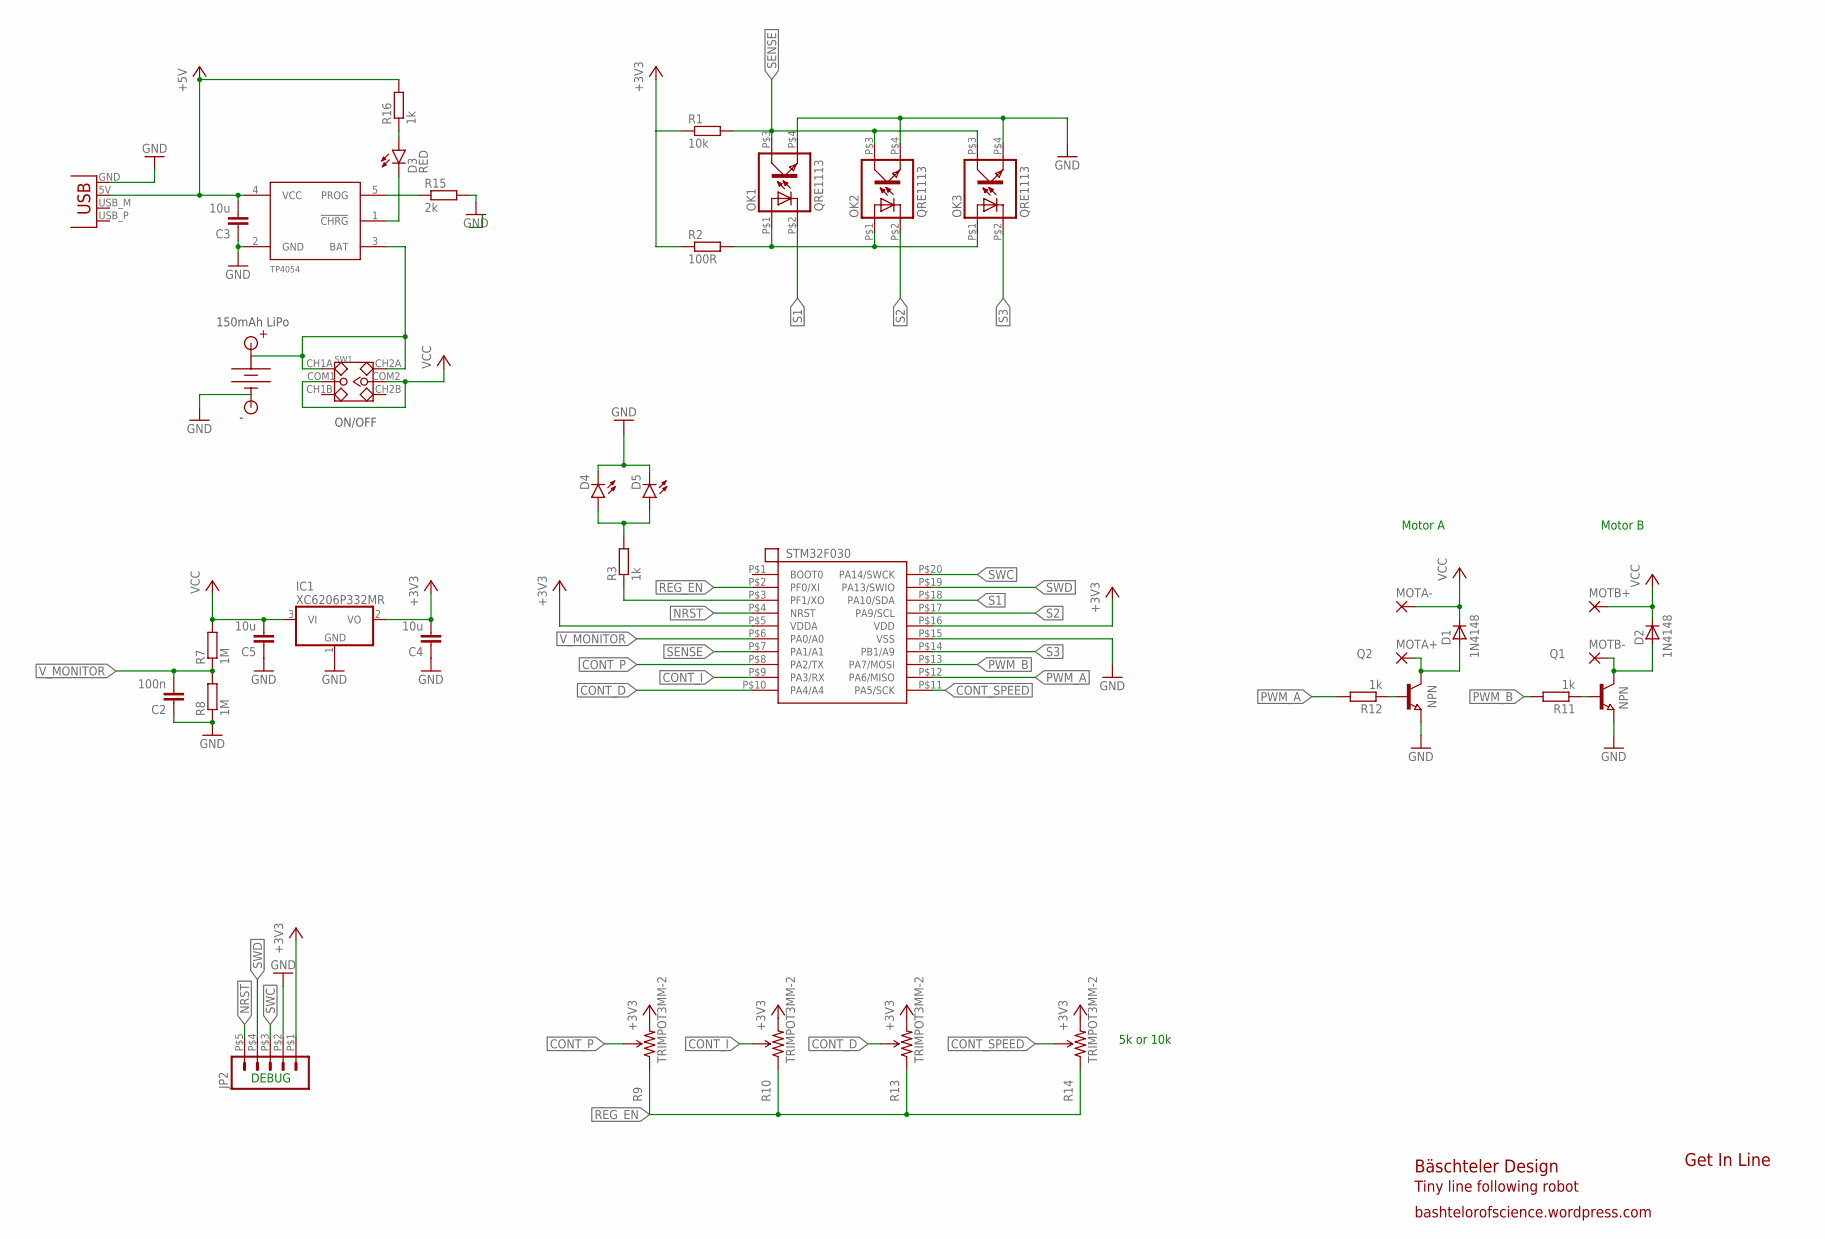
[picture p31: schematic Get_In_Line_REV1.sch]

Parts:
C2: 100n; C0805
C3, C4, C5: 10u; C0805
D1, D2: D-SOD-80; SOD80
D3: RED; LED-1206
D4, D5: GREEN; LED-1206
IC1: MCP1703CB; SOT23
JP1: USBPCB; USB-A-PCB
JP2: M05; SMD_HEADER_5P
MCU: STM32F030F4P6; TSSOP-20
MOTA+: 1,6/0,9
MOTA-: 1,6/0,9
MOTB+: 1,6/0,9
MOTB-: 1,6/0,9
OK1, OK2, OK3: QRE1113; DIL04
Q1, Q2: NPN-TRANSISTOR_SOT23; SOT23
R1: 10k; R0805
R2: 100R; R0805
R3, R11, R12, R16: 1k; R0805
R7, R8: 1M; R0805
R9, R10, R13, R14: TRIMPOT3MM-2; TRIMPOT-3MM-2
R15: 2k; R0805
SW1: DIP-TOGGLE-SWITCH-2CH-(2X3P-2.54); SW6-2.54-9.0X3.5X3.2+2.0MM
U$1: TP4054_LIPO_CHARGER; SOT23-5
U$5: BATTERY_PAD+1.5MM; LIPO_BATTERY_PADS_1.5MM
U$6: BATTERY_PAD-1.5MM; LIPO_BATTERY_PADS_1.5MM

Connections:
+3V3: C4.2, IC1.2 (VO), JP2.P$1 (1), MCU.P$5 (VDDA), MCU.P$16 (VDD), R1.1, R2.1, R9.3 (CW), R10.3 (CW), R13.3 (CW), R14.3 (CW)
+5V: C3.2, JP1.5V (VBUS), R16.2, U$1.4 (VCC)
CONT_D: MCU.P$10 (PA4/A4), R13.2 (WIPER)
CONT_I: MCU.P$9 (PA3/RX), R10.2 (WIPER)
CONT_P: MCU.P$8 (PA2/TX), R9.2 (WIPER)
CONT_SPEED: MCU.P$11 (PA5/SCK), R14.2 (WIPER)
GND: C2.1, C3.1, C4.1, C5.1, D4.C, D5.C, IC1.1 (GND), JP1.GND, JP2.P$2 (2), MCU.P$15 (VSS), OK1.P$4 (EMIT), OK2.P$4 (EMIT), OK3.P$4 (EMIT), Q1.2 (E), Q2.2 (E), R8.1, R15.2, U$1.2 (GND), U$6.P$1
LED: MCU.P$3 (PF1/XO), R3.1
LEDOUT: D4.A, D5.A, R3.2
unnamed: OK1.P$1 (A), OK2.P$1 (A), OK3.P$1 (A), R2.2
unnamed: R15.1, U$1.5 (PROG)
unnamed: D3.C, U$1.1 (!CHRG)
unnamed: D3.A, R16.1
unnamed: Q1.1 (B), R11.1
unnamed: Q2.1 (B), R12.1
unnamed: D1.2 (A), MOTA+.1, Q2.3 (C)
unnamed: D2.2 (A), MOTB-.1, Q1.3 (C)
NRST: JP2.P$5 (5), MCU.P$4 (NRST)
PWM_A: MCU.P$12 (PA6/MISO), R12.2
PWM_B: MCU.P$13 (PA7/MOSI), R11.2
REG_EN: MCU.P$2 (PF0/XI), R9.1 (CCW), R10.1 (CCW), R13.1 (CCW), R14.1 (CCW)
S1: MCU.P$18 (PA10/SDA), OK1.P$2 (C)
S2: MCU.P$17 (PA9/SCL), OK2.P$2 (C)
S3: MCU.P$14 (PB1/A9), OK3.P$2 (C)
SENSE: MCU.P$7 (PA1/A1), OK1.P$3 (COL), OK2.P$3 (COL), OK3.P$3 (COL), R1.2
SWC: JP2.P$3 (3), MCU.P$20 (PA14/SWCK)
SWD: JP2.P$4 (4), MCU.P$19 (PA13/SWIO)
VBAT: SW1.CH1A, SW1.CH2A, U$1.3 (BAT), U$5.P$1
VCC: C5.2, D1.1 (C), D2.1 (C), IC1.3 (VI), MOTA-.1, MOTB+.1, R7.2, SW1.COM1, SW1.COM2
V_MONITOR: C2.2, MCU.P$6 (PA0/A0), R7.1, R8.2

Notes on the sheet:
Motor A
Motor B
1N4148
XC6206P332MR
DEBUG
ON/OFF
5k or 10k
Get In Line
Bäschteler Design
bashtelorofscience.wordpress.com
Tiny line following robot
STM32F030
NPN
150mAh LiPo

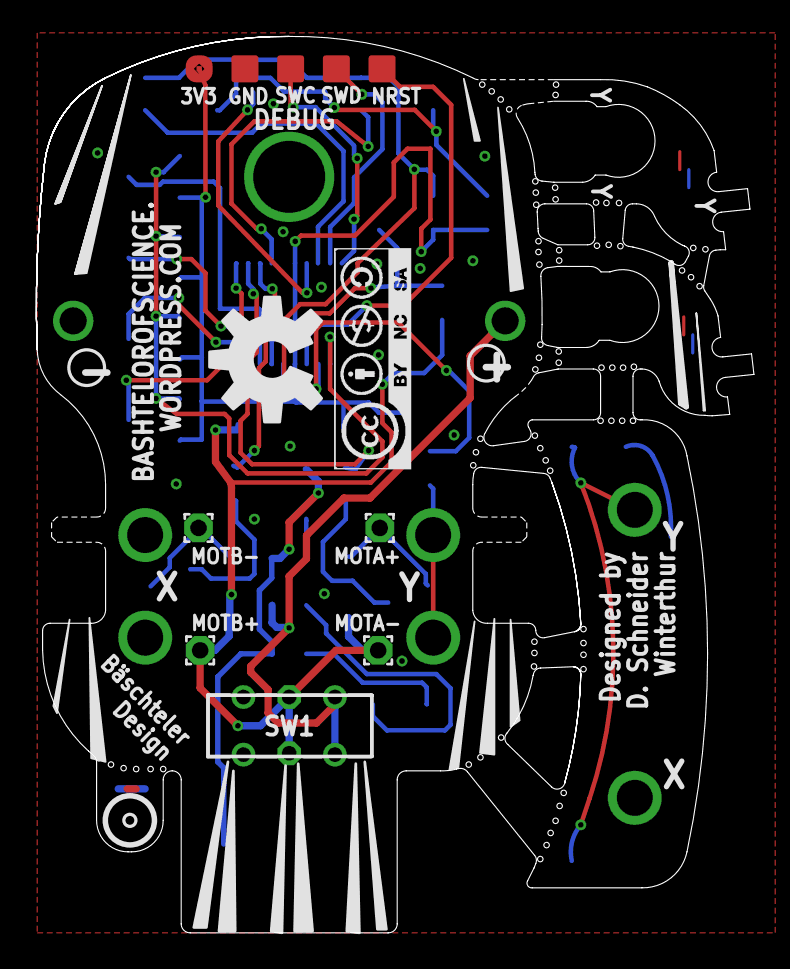
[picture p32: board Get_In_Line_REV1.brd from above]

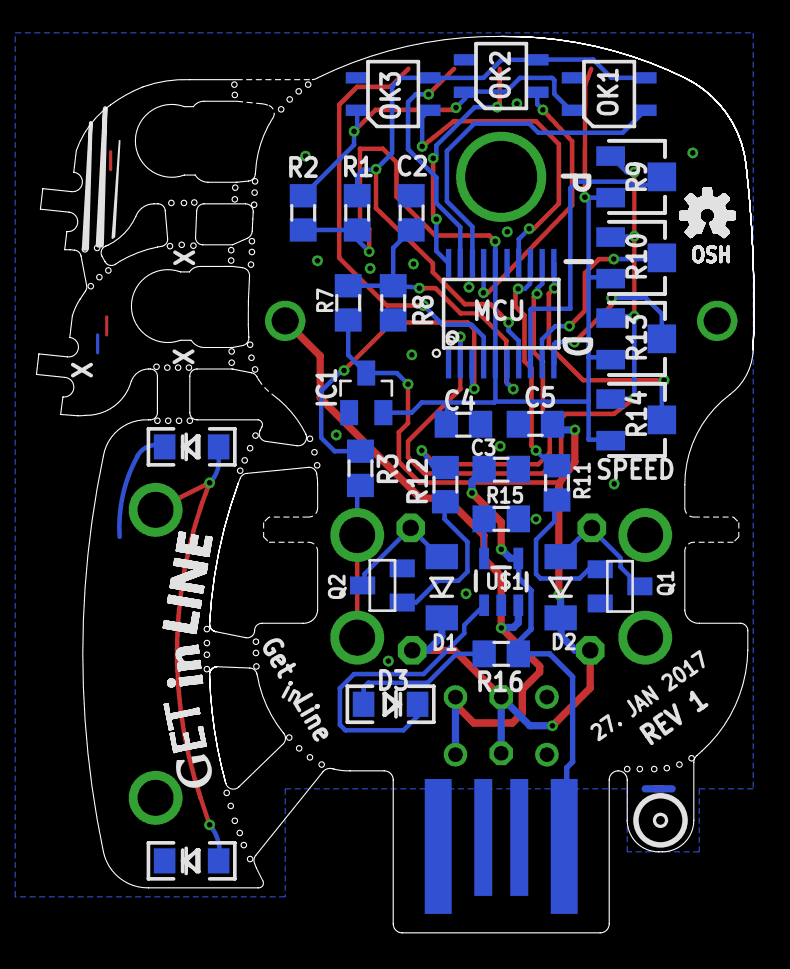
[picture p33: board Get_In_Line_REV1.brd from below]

Board: 2 copper layers, 39.9 x 49.8 mm, 49 parts (39 on the bottom side), 30 nets.

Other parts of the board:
U$2, U$8, U$9, U$10, U$13, U$14, U$15, U$16: OSHW-LOGO-S
U$4: CC-BY-NC-SA
U$33: OSHW-LOGO-L

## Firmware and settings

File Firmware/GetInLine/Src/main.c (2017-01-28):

/**
 ******************************************************************************
 * File Name          : main.c
 * Description        : Main program body
 ******************************************************************************
 *
 * COPYRIGHT(c) 2017 STMicroelectronics
 *
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
 ******************************************************************************
 */
/* Includes ------------------------------------------------------------------*/
#include "main.h"
#include "stm32f0xx_hal.h"

/* USER CODE BEGIN Includes */
#include "globals.h"
#include "control.h"
/* USER CODE END Includes */

ADC_HandleTypeDef hadc;

TIM_HandleTypeDef htim3;

/* USER CODE BEGIN PV */
enum {
	ADC_SAMPLING, ADC_COMPLETE, ADC_ERROR
};

uint16_t newADCValue; //ADC interrupt mode: callback writes new value to this variable
uint8_t ADCstatusFlag = ADC_COMPLETE; //flag is set before starting ADC sampling, cleared in the ADC interrupt

/* USER CODE END PV */

void SystemClock_Config(void);
void Error_Handler(void);
static void MX_GPIO_Init(void);
static void MX_ADC_Init(void);
static void MX_TIM3_Init(void);
static void MX_NVIC_Init(void);

void HAL_TIM_MspPostInit(TIM_HandleTypeDef *htim);

/* USER CODE BEGIN PFP */

/* USER CODE END PFP */

/* USER CODE BEGIN 0 */

/*
 * Get-In-Line line follower firware
 *
 here is how the initial version should work:

 initialize everything
 in the main loop:
 -read all analog input channels (can deactivate some channels if this is not fast enough)
 -calculate the position of the line using interpolation algorithm
 -adjust PWM values of the motors according to PID parameters to get the line to the center
 -if no line is detected go straight ahead

 advanced stuff for later:
 -adjust pwm value according to input voltage to not make the robot slow down on lower input voltage
 -maybe need some algorithm to detect crossings -> line width is bigger than usual
 -also maybe need an algorithm to detect right angles



 *
 */

/* USER CODE END 0 */

int main(void) {

	/* USER CODE BEGIN 1 */
	/*

	 Warning:
	 --------
	 The initialization setup is done in CubeMX, code outside of 'USER CODE' sections
	 is removed when re-generating the code. Keep any user functions within these sections.

	 */
	/* USER CODE END 1 */

	/* MCU Configuration----------------------------------------------------------*/

	/* Reset of all peripherals, Initializes the Flash interface and the Systick. */
	HAL_Init();

	/* Configure the system clock */
	SystemClock_Config();

	/* Initialize all configured peripherals */
	MX_GPIO_Init();
	MX_ADC_Init();
	MX_TIM3_Init();

	/* Initialize interrupts */
	MX_NVIC_Init();

	/* USER CODE BEGIN 2 */

	//do some blinking to show proper boot
	HAL_Delay(200);
	LED_ON;
	HAL_Delay(200);
	LED_OFF;
	HAL_Delay(150);
	LED_ON;
	HAL_Delay(150);
	LED_OFF;
	HAL_Delay(100);
	LED_ON;
	HAL_Delay(100);
	LED_OFF;
	HAL_Delay(50);
	LED_ON;
	readAllADCs(); //reads all ADC channels and deactivates all but the sensor channel afterwards
//	readAllADCs(); //read ADCs again (first time read gets wrong value on vrefint
	LED_OFF;

	/* USER CODE END 2 */

	/* Infinite loop */
	/* USER CODE BEGIN WHILE */

	uint32_t timestamp = HAL_GetTick();

	while (1) {

		RobotControl(); //run the controller periodically as fast as possible

		//HAL_Delay(1);
		if (HAL_GetTick() - timestamp > 100) {
			timestamp = HAL_GetTick();
			readAllADCs();
		}

	}
	/* USER CODE END WHILE */

}

/** System Clock Configuration
 */
void SystemClock_Config(void) {

	RCC_OscInitTypeDef RCC_OscInitStruct;
	RCC_ClkInitTypeDef RCC_ClkInitStruct;

	/**Initializes the CPU, AHB and APB busses clocks
	 */
	RCC_OscInitStruct.OscillatorType = RCC_OSCILLATORTYPE_HSI
			| RCC_OSCILLATORTYPE_HSI14;
	RCC_OscInitStruct.HSIState = RCC_HSI_ON;
	RCC_OscInitStruct.HSI14State = RCC_HSI14_ON;
	RCC_OscInitStruct.HSICalibrationValue = 16;
	RCC_OscInitStruct.HSI14CalibrationValue = 16;
	RCC_OscInitStruct.PLL.PLLState = RCC_PLL_NONE;
	if (HAL_RCC_OscConfig(&RCC_OscInitStruct) != HAL_OK) {
		Error_Handler();
	}

	/**Initializes the CPU, AHB and APB busses clocks
	 */
	RCC_ClkInitStruct.ClockType = RCC_CLOCKTYPE_HCLK | RCC_CLOCKTYPE_SYSCLK
			| RCC_CLOCKTYPE_PCLK1;
	RCC_ClkInitStruct.SYSCLKSource = RCC_SYSCLKSOURCE_HSI;
	RCC_ClkInitStruct.AHBCLKDivider = RCC_SYSCLK_DIV1;
	RCC_ClkInitStruct.APB1CLKDivider = RCC_HCLK_DIV1;

	if (HAL_RCC_ClockConfig(&RCC_ClkInitStruct, FLASH_LATENCY_0) != HAL_OK) {
		Error_Handler();
	}

	/**Configure the Systick interrupt time
	 */
	HAL_SYSTICK_Config(HAL_RCC_GetHCLKFreq() / 1000);

	/**Configure the Systick
	 */
	HAL_SYSTICK_CLKSourceConfig(SYSTICK_CLKSOURCE_HCLK);

	/* SysTick_IRQn interrupt configuration */
	HAL_NVIC_SetPriority(SysTick_IRQn, 0, 0);
}

/** NVIC Configuration
 */
static void MX_NVIC_Init(void) {
	/* ADC1_IRQn interrupt configuration */
	HAL_NVIC_SetPriority(ADC1_IRQn, 0, 0);
	HAL_NVIC_EnableIRQ(ADC1_IRQn);
}

/* ADC init function */
static void MX_ADC_Init(void) {

	ADC_ChannelConfTypeDef sConfig;

	/**Configure the global features of the ADC (Clock, Resolution, Data Alignment and number of conversion)
	 */
	hadc.Instance = ADC1;
	hadc.Init.ClockPrescaler = ADC_CLOCK_ASYNC_DIV1;
	hadc.Init.Resolution = ADC_RESOLUTION_12B;
	hadc.Init.DataAlign = ADC_DATAALIGN_RIGHT;
	hadc.Init.ScanConvMode = ADC_SCAN_DIRECTION_FORWARD;
	hadc.Init.EOCSelection = ADC_EOC_SINGLE_CONV;
	hadc.Init.LowPowerAutoWait = DISABLE;
	hadc.Init.LowPowerAutoPowerOff = DISABLE;
	hadc.Init.ContinuousConvMode = DISABLE;
	hadc.Init.DiscontinuousConvMode = ENABLE;
	hadc.Init.ExternalTrigConv = ADC_SOFTWARE_START;
	hadc.Init.ExternalTrigConvEdge = ADC_EXTERNALTRIGCONVEDGE_NONE;
	hadc.Init.DMAContinuousRequests = DISABLE;
	hadc.Init.Overrun = ADC_OVR_DATA_OVERWRITTEN;
	if (HAL_ADC_Init(&hadc) != HAL_OK) {
		Error_Handler();
	}

	/**Configure for the selected ADC regular channel to be converted.
	 */
	sConfig.Channel = ADC_CHANNEL_0;
	sConfig.Rank = ADC_RANK_CHANNEL_NUMBER;
	sConfig.SamplingTime = ADC_SAMPLETIME_55CYCLES_5;
	if (HAL_ADC_ConfigChannel(&hadc, &sConfig) != HAL_OK) {
		Error_Handler();
	}

	/**Configure for the selected ADC regular channel to be converted.
	 */
	sConfig.Channel = ADC_CHANNEL_1;
	if (HAL_ADC_ConfigChannel(&hadc, &sConfig) != HAL_OK) {
		Error_Handler();
	}

	/**Configure for the selected ADC regular channel to be converted.
	 */
	sConfig.Channel = ADC_CHANNEL_2;
	if (HAL_ADC_ConfigChannel(&hadc, &sConfig) != HAL_OK) {
		Error_Handler();
	}

	/**Configure for the selected ADC regular channel to be converted.
	 */
	sConfig.Channel = ADC_CHANNEL_3;
	if (HAL_ADC_ConfigChannel(&hadc, &sConfig) != HAL_OK) {
		Error_Handler();
	}

	/**Configure for the selected ADC regular channel to be converted.
	 */
	sConfig.Channel = ADC_CHANNEL_4;
	if (HAL_ADC_ConfigChannel(&hadc, &sConfig) != HAL_OK) {
		Error_Handler();
	}

	/**Configure for the selected ADC regular channel to be converted.
	 */
	sConfig.Channel = ADC_CHANNEL_5;
	if (HAL_ADC_ConfigChannel(&hadc, &sConfig) != HAL_OK) {
		Error_Handler();
	}

	/**Configure for the selected ADC regular channel to be converted.
	 */
	sConfig.Channel = ADC_CHANNEL_VREFINT;
	if (HAL_ADC_ConfigChannel(&hadc, &sConfig) != HAL_OK) {
		Error_Handler();
	}

}

/* TIM3 init function */
static void MX_TIM3_Init(void) {

	TIM_MasterConfigTypeDef sMasterConfig;
	TIM_OC_InitTypeDef sConfigOC;

	htim3.Instance = TIM3;
	htim3.Init.Prescaler = 0;
	htim3.Init.CounterMode = TIM_COUNTERMODE_UP;
	htim3.Init.Period = 512;
	htim3.Init.ClockDivision = TIM_CLOCKDIVISION_DIV1;
	htim3.Init.AutoReloadPreload = TIM_AUTORELOAD_PRELOAD_DISABLE;
	if (HAL_TIM_PWM_Init(&htim3) != HAL_OK) {
		Error_Handler();
	}

	sMasterConfig.MasterOutputTrigger = TIM_TRGO_RESET;
	sMasterConfig.MasterSlaveMode = TIM_MASTERSLAVEMODE_DISABLE;
	if (HAL_TIMEx_MasterConfigSynchronization(&htim3, &sMasterConfig)
			!= HAL_OK) {
		Error_Handler();
	}

	sConfigOC.OCMode = TIM_OCMODE_PWM1;
	sConfigOC.Pulse = 0;
	sConfigOC.OCPolarity = TIM_OCPOLARITY_HIGH;
	sConfigOC.OCFastMode = TIM_OCFAST_DISABLE;
	if (HAL_TIM_PWM_ConfigChannel(&htim3, &sConfigOC, TIM_CHANNEL_1)
			!= HAL_OK) {
		Error_Handler();
	}

	if (HAL_TIM_PWM_ConfigChannel(&htim3, &sConfigOC, TIM_CHANNEL_2)
			!= HAL_OK) {
		Error_Handler();
	}

	HAL_TIM_MspPostInit(&htim3);

}

/** Configure pins as 
 * Analog
 * Input
 * Output
 * EVENT_OUT
 * EXTI
 */
static void MX_GPIO_Init(void) {

	GPIO_InitTypeDef GPIO_InitStruct;

	/* GPIO Ports Clock Enable */
	__HAL_RCC_GPIOF_CLK_ENABLE()
	;
	__HAL_RCC_GPIOA_CLK_ENABLE()
	;
	__HAL_RCC_GPIOB_CLK_ENABLE()
	;

	/*Configure GPIO pin Output Level */
	HAL_GPIO_WritePin(GPIOF, GPIO_PIN_0 | GPIO_PIN_1, GPIO_PIN_RESET);

	/*Configure GPIO pin Output Level */
	HAL_GPIO_WritePin(GPIOB, GPIO_PIN_1, GPIO_PIN_SET);

	/*Configure GPIO pin Output Level */
	HAL_GPIO_WritePin(GPIOA, GPIO_PIN_9 | GPIO_PIN_10, GPIO_PIN_SET);

	/*Configure GPIO pins : PF0 PF1 */
	GPIO_InitStruct.Pin = GPIO_PIN_0 | GPIO_PIN_1;
	GPIO_InitStruct.Mode = GPIO_MODE_OUTPUT_PP;
	GPIO_InitStruct.Pull = GPIO_NOPULL;
	GPIO_InitStruct.Speed = GPIO_SPEED_FREQ_LOW;
	HAL_GPIO_Init(GPIOF, &GPIO_InitStruct);

	/*Configure GPIO pin : PB1 */
	GPIO_InitStruct.Pin = GPIO_PIN_1;
	GPIO_InitStruct.Mode = GPIO_MODE_OUTPUT_PP;
	GPIO_InitStruct.Pull = GPIO_NOPULL;
	GPIO_InitStruct.Speed = GPIO_SPEED_FREQ_HIGH;
	HAL_GPIO_Init(GPIOB, &GPIO_InitStruct);

	/*Configure GPIO pins : PA9 PA10 */
	GPIO_InitStruct.Pin = GPIO_PIN_9 | GPIO_PIN_10;
	GPIO_InitStruct.Mode = GPIO_MODE_OUTPUT_PP;
	GPIO_InitStruct.Pull = GPIO_NOPULL;
	GPIO_InitStruct.Speed = GPIO_SPEED_FREQ_HIGH;
	HAL_GPIO_Init(GPIOA, &GPIO_InitStruct);

}

/* USER CODE BEGIN 4 */
void HAL_ADC_ConvCpltCallback(ADC_HandleTypeDef* hadc) {
	newADCValue = HAL_ADC_GetValue(hadc);
	ADCstatusFlag = ADC_COMPLETE;
}

//read one ADC value from current channel, channels are automatically changed after each read (up counting)
uint16_t ADC_readValue(void) {
	if (ADCstatusFlag != ADC_SAMPLING) {
		ADCstatusFlag = ADC_SAMPLING;

		/*
		 //use interrupt to sample the ADC (somehow not working...)
		 HAL_ADC_Start_IT(&hadc);
		 while (ADCstatusFlag == ADC_SAMPLING) {
		 //HAL_PWR_EnterSLEEPMode(PWR_MAINREGULATOR_ON, PWR_SLEEPENTRY_WFI);
		 }*/

		HAL_ADC_Start(&hadc);
		HAL_ADC_PollForConversion(&hadc, 5);
		newADCValue = HAL_ADC_GetValue(&hadc);
		ADCstatusFlag = ADC_COMPLETE;
		return newADCValue;
	} else
		return -1;
}

void readAllADCs(void) {
	//read all ADC channels once, this is done once every few seconds
	//the ADC is re-initialized to ensure the reading starts at channel 0 (I did not find another way to select the next channel to be converted)
	//after all channels are read, all channels except the optical sensor channel are disbled again
	ADC_ChannelConfTypeDef sConfig;
	volatile uint16_t VrefInt;

	//(re-)activate all channels
	sConfig.Rank = ADC_RANK_CHANNEL_NUMBER; //enable channel ranks
	sConfig.Channel = ADC_CHANNEL_0;
	HAL_ADC_ConfigChannel(&hadc, &sConfig);
	sConfig.Channel = ADC_CHANNEL_2;
	HAL_ADC_ConfigChannel(&hadc, &sConfig);
	sConfig.Channel = ADC_CHANNEL_3;
	HAL_ADC_ConfigChannel(&hadc, &sConfig);
	sConfig.Channel = ADC_CHANNEL_4;
	HAL_ADC_ConfigChannel(&hadc, &sConfig);
	sConfig.Channel = ADC_CHANNEL_5;
	HAL_ADC_ConfigChannel(&hadc, &sConfig);
	sConfig.Channel = ADC_CHANNEL_VREFINT;
	HAL_ADC_ConfigChannel(&hadc, &sConfig);

	//channels are: voltage, sensor, P,I,D, speed, Vref internal (7 channels total)
	Vbat = ADC_readValue();
	ADC_readValue(); //sensor value is not needed, read and discard it
	potentiometers[0] = ADC_readValue(); //P
	potentiometers[1] = ADC_readValue(); //I
	potentiometers[2] = ADC_readValue(); //D
	potentiometers[3] = ADC_readValue(); //speed
	VrefInt = ADC_readValue();

	//calculate the actual battery voltage level from internal reference
	volatile uint32_t inputVoltage = ((uint32_t) (*VREFINT_CAL_ADDR)
			* (uint32_t) 3300) / (uint32_t) VrefInt;

	Vbat = ((uint32_t) 3200 * 2 * (uint32_t) Vbat) / (uint32_t) 4095; //external voltage in millivolts (times 2 because of voltage divider)

	//disable sampling on all channels except channel 1 (sensor input channel)

	sConfig.Rank = ADC_RANK_NONE; //disable channel rank (channel will not be sampled)
	sConfig.Channel = ADC_CHANNEL_0;
	HAL_ADC_ConfigChannel(&hadc, &sConfig);
	sConfig.Channel = ADC_CHANNEL_2;
	HAL_ADC_ConfigChannel(&hadc, &sConfig);
	sConfig.Channel = ADC_CHANNEL_3;
	HAL_ADC_ConfigChannel(&hadc, &sConfig);
	sConfig.Channel = ADC_CHANNEL_4;
	HAL_ADC_ConfigChannel(&hadc, &sConfig);
	sConfig.Channel = ADC_CHANNEL_5;
	HAL_ADC_ConfigChannel(&hadc, &sConfig);
	sConfig.Channel = ADC_CHANNEL_VREFINT;
	HAL_ADC_ConfigChannel(&hadc, &sConfig);
}

/* USER CODE END 4 */
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


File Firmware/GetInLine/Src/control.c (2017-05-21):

/*
 File: control.c
 Part of the 'Get In Line' line follower

 The MIT License (MIT)

 Copyright (c) 2017 Damian Schneider

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
 this file contains the algorithms to control the robot
 */
#include "stm32f0xx_hal.h"
#include "globals.h"
#include "setup.h"

#define SENSORSPACING 7500 //sensor x-spacing in micrometers
#define ANTIWINDUP_MAX 900 //maximum allowed value for the integrator

//interpolation algorithm for the three sensor values. line position is micrometers from the center (positive is right, negative left)
int16_t calculateLinePosition(void) {
	int16_t lineposition;
	static int16_t lastlineposition = 5000;
	static int16_t calibrate_countdown = 500; //take 500 measurements to calibrate, then stop

	static uint16_t sensorminvalue[3] = { 2000, 2000, 2000 }; //minimum value seen by each sensor (start with a high value)

	//save the minimum sensorvalues and use them as a sensor calibration bias
	uint8_t i;
	if (calibrate_countdown) //only calibrate at the beginning
	{
		if (sensorValues[0] < 3400 && sensorValues[1] < 3400
				&& sensorValues[2] < 3400) { //if actually on the ground in a whiteish environment
			for (i = 0; i < 3; i++) {
				if (sensorValues[i] < sensorminvalue[i]) {
					sensorminvalue[i] =
							(8 * sensorminvalue[i] + (uint16_t)sensorValues[i]) / 9; //use simple lowpass filter
				}
				//calibrate the sensor value (deduct the minimum value, sensorvalue must never be negative!)
				//sensorValues[i]=((uint32_t)sensorValues[i]<<10)/ sensorminvalue[i];

			}
			calibrate_countdown--;
		}
	}
	//apply calibration data
	for (i = 0; i < 3; i++) {
	sensorValues[i] -= sensorminvalue[i];
	if (sensorValues[i] < 0)
		sensorValues[i] = 0;
	}
	//the line position is the weighted average of the sensor values:
	//weighted with the position, position of the left sensor is taken as 'SENSORSPACING' since 0 is not a good idea

	uint32_t weightedsum = SENSORSPACING * (uint32_t) sensorValues[0]
			+ 2 * SENSORSPACING * (uint32_t) sensorValues[1]
			+ 3 * SENSORSPACING * (uint32_t) sensorValues[2];

	uint32_t weightedavg = weightedsum
			/ ((uint32_t) sensorValues[0] + (uint32_t) sensorValues[1]
					+ (uint32_t) sensorValues[2]);
	//now we have the weighted average of the position but with an offset (zero position is one SENSORSPACING to the left of the left sensor)
	//deduct two SENSORSPACINGS to offset to the center position
	lineposition = (int32_t) weightedavg - 2 * (int32_t) SENSORSPACING;
	/*
	 //if line position error is small, check if line is moving out of sight
	 if (lineposition < 1000 && lineposition > -1000) {
	 if (sensorValues[1] - sensorminvalue[1] < 1000) //line is out of sight from the central sensor
	 {
	 if (lineposition < 300 && lineposition > -300) {
	 lineposition_state = POSITION_BAD; //completely out of sight
	 lineposition = lastlineposition;
	 } else if (lineposition_state != POSITION_BAD) { //cannot go from bad to critical
	 lineposition_state = POSITION_CRITICAL; //line is on the outer edge of field of view
	 if (lineposition > 0)
	 lineposition = SENSORSPACING / 2;
	 else
	 lineposition = -SENSORSPACING / 2;

	 lastlineposition = lineposition;
	 }
	 }
	 } else //if position error is big, the line is in sight
	 {
	 lineposition_state = POSITION_OK;
	 lastlineposition = lineposition;
	 }*/
	//if sum of all sensor values is small, we lost sight of the line
	if (sensorValues[0] + sensorValues[1] + sensorValues[2] < 1400) {
		lineposition_state = POSITION_BAD; //completely out of sight
		if(lastlineposition>0)lineposition = SENSORSPACING / 2;
		else lineposition = -SENSORSPACING / 2;

	} else //if at least one sensor shows a high value, there is a line
	{
		lineposition_state = POSITION_OK;
		lastlineposition = lineposition;
	}
	return lineposition;
}

//PID regulator:
//the regulator tries to get the line to the zero position by changing the
//speeds of the motors proportionally to the offset error (P-regulator)
//the added integral of the error removes the offset any P-regulator has
//the differential part acts as a 'damping' effect for the integral part and also does a 'look ahead' (by looking at change of error rather than the error itself)
//the ideal parameters are found by experimentation. The code must set some limits to the PID parameters (kp, ki, kd) but the parameters themselves are set by the potentiometers

//input to the regulator is the error of the position, output is the amount of 'steering' needed

int32_t PIDregulator(int16_t error) {
	static int16_t lasterror; //to calculate the differential
	static int16_t integratederror = 0; //the calculated integral
	static int16_t differential;
//	static int32_t differentiallowpass = 0;
	int32_t output;

	volatile int32_t P;
	volatile int32_t I;
	volatile int32_t D;

	//calculate the integral
	integratederror += error;
	if (integratederror > ANTIWINDUP_MAX)
		integratederror = ANTIWINDUP_MAX;
	if (integratederror < -ANTIWINDUP_MAX)
		integratederror = -ANTIWINDUP_MAX;
	/*
	 //reset the integrated error when crossing the center
	 if ((lasterror > 0 && error < 0) || (lasterror < 0 && error > 0))
	 integratederror = 0;
	 */
	if (lineposition_state == POSITION_OK) {
		integratederror = 0;
	}

	/*
	 //bring the integrated error back to zero over time (damping)
	 if (integratederror > 7)
	 integratederror -= 15;
	 else if (integratederror < -7)
	 integratederror += 15;
	 */
	//calculate the differential
	differential = (differential + (lasterror - error)) / 2;
	//use a lowpass to even out spikes in readings: output = (x * last_output + present_reading) / (x+1)
	//differentiallowpass = ((7*differentiallowpass)+(int32_t (lasterror - error)))>>3;

	lasterror = error;

	//PID regulator with cubed proportional output
	//P = (int32_t) potentiometers[0] * error* error * error;
	//if(error < 0) P = -P;
	//I = (int32_t) (potentiometers[1]<<5) * integratederror;
	//D = (int32_t) (potentiometers[2]<<2) * differential;
	P = (int32_t) (potentiometers[0]>>1) * error;
	//if(error < 0) P = -P;
	I = (int32_t) (potentiometers[1] >> 2) * integratederror;
	D = (int32_t) (potentiometers[2] >> 2) * differential;
	//D = 0;

	//I=0;
	output = P + I + D;

	return output;
}
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

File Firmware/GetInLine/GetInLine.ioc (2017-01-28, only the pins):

Mcu.UserName=STM32F030F4Px
PA0.Signal=ADC_IN0
PA1.Signal=ADC_IN1
PA10.Signal=GPIO_Output
PA13.Signal=SYS_SWDIO
PA14.Signal=SYS_SWCLK
PA2.Signal=ADC_IN2
PA3.Signal=ADC_IN3
PA4.Signal=ADC_IN4
PA5.Signal=ADC_IN5
PA6.Signal=S_TIM3_CH1
PA7.Signal=S_TIM3_CH2
PA9.Signal=GPIO_Output
PB1.Signal=GPIO_Output
PF0-OSC_IN.Signal=GPIO_Output
PF1-OSC_OUT.Signal=GPIO_Output

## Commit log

2017-01-28 Initial commit
    initial commit of repository
    [.custom.cfg, GetInLine.cfg, GetInLine_F0.cfg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]
2017-05-21 regulator improvements
    improved the regulator and added sensor self-calibration so the code
    runs well on all robots, not just the first prorotype.
2017-05-21 minor fix
    [Get_In_Line_REV1.brd]

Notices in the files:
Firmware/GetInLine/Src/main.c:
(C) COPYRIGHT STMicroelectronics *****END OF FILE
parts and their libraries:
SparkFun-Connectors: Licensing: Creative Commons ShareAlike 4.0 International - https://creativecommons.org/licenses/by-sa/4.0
